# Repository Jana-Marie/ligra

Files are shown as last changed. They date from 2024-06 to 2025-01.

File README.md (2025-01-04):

# ligra

ligra is an open source image projector build from scratch and based off of flea market parts. ligra is not neccessarily a PCB-project nor a single thing, but rather an idea of how to design your own image-projection system. It is an introduction on how to create light-grafittis, how to share messages at large.

It's not strictly a Gobo, rather a way of building a system that may resemble one, but may also resemble a video projector or an abstract source of art. I have mostly used it with 2D printed stencils, usually used with so called "overhead projectors", one can of course also use metal-stencils, coloured effect-foils, 3D printed stencils and even LCDs, or really anything that may project an image. Get creative! 

<table>
  <tbody>
    <tr>
      <td>
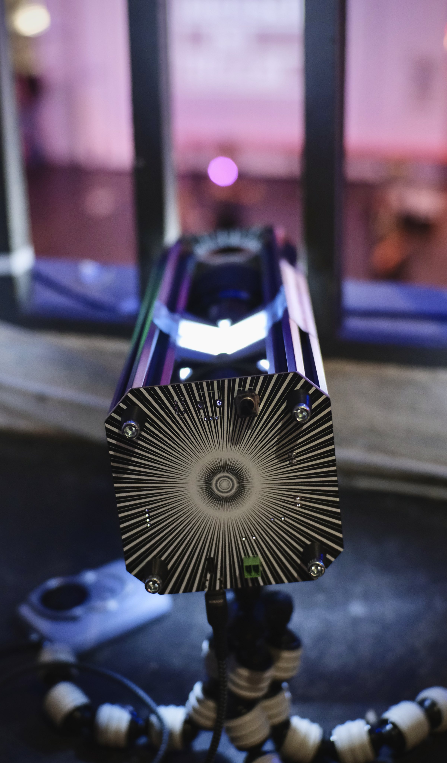
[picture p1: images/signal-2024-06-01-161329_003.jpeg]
        
      </td>
      <td>
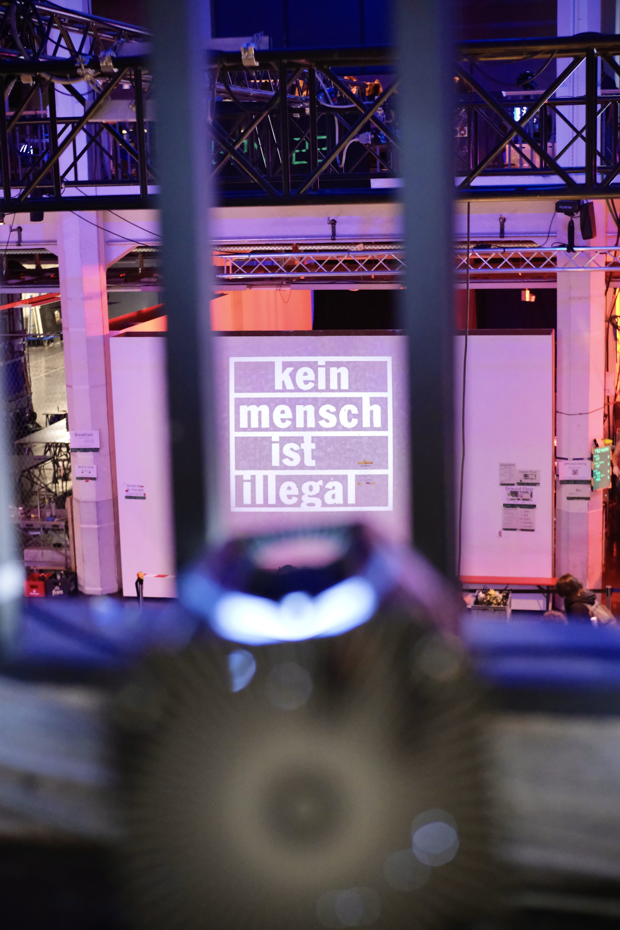
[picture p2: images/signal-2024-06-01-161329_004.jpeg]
        
      </td>
    </tr>
    <tr>
      <td colspan="2">
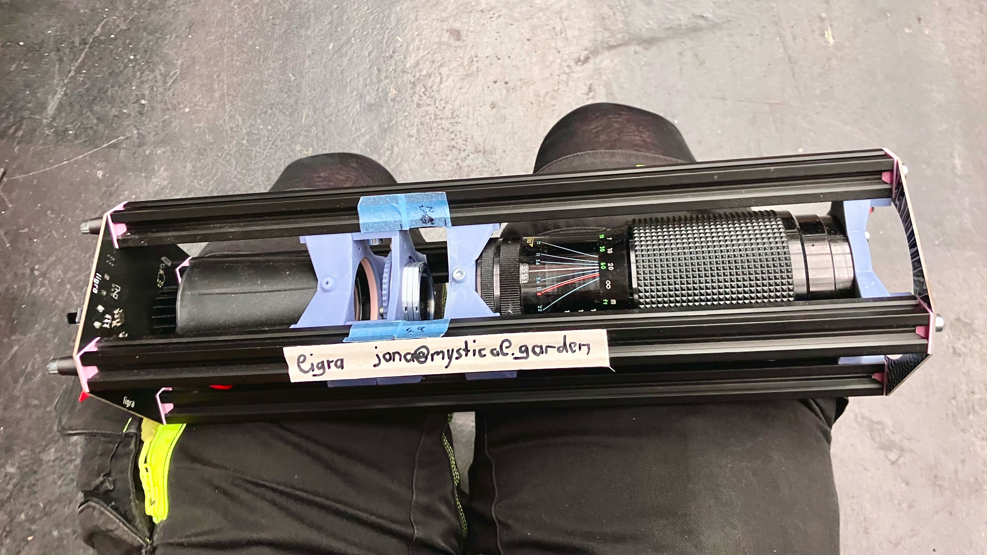
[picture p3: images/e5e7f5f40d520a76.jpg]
        
      </td>
    </tr>
  </tbody>
</table>

This repo is very WIP and shall be expanded soon :3

## Working principle

ligra essentially functions as a backwards camera, well, most projectors do. This becomes more visible when we talk about its inner workings, it's heart and most fixed element is the lens, a Canon FD lens in our case. But instead of using it to project and image **onto** a 35mm film slide, we will project light **through** a ruffly 35mm film slide-sized, image forming medium (i.e. a 2D printed stencil). This light will enter the lens from the back, projecting an image onto a scene with the properties of the lens (focal length, aperture and focus). Given the quality of even early lenses, we can expect some sharp and crisp projections. [WIP ...]

## [Instructions](https://github.com/Jana-Marie/ligra/blob/main/instructions.md)

(Want to build one? ^ click me)

<table>
  <tbody>
    <tr>
      <td>
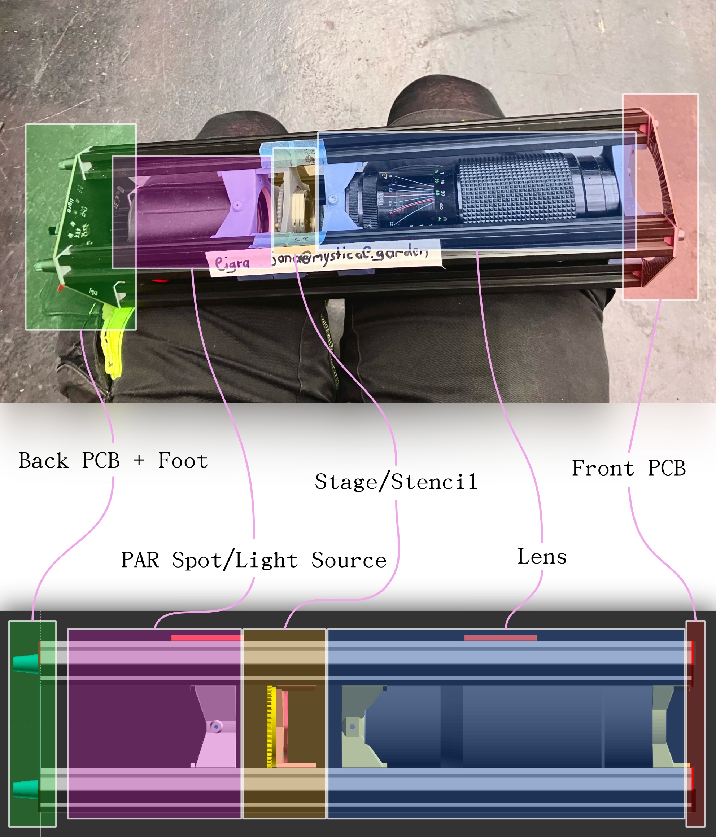
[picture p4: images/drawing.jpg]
        
      </td>
    </tr>
  </tbody>
</table>

## [Projection-Media](https://github.com/Jana-Marie/ligra/blob/main/projection-media.md)

(You have one and need stencils? ^ click me)

<table>
  <tbody>
    <tr>
      <td>
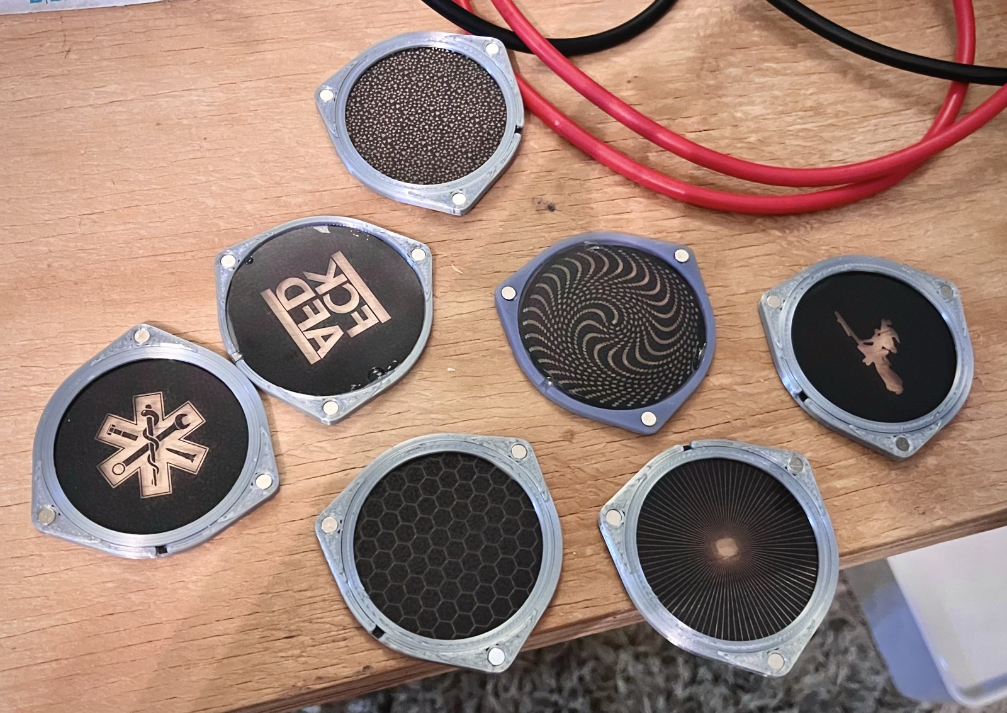
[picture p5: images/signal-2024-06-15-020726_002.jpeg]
        
      </td>
      <td>
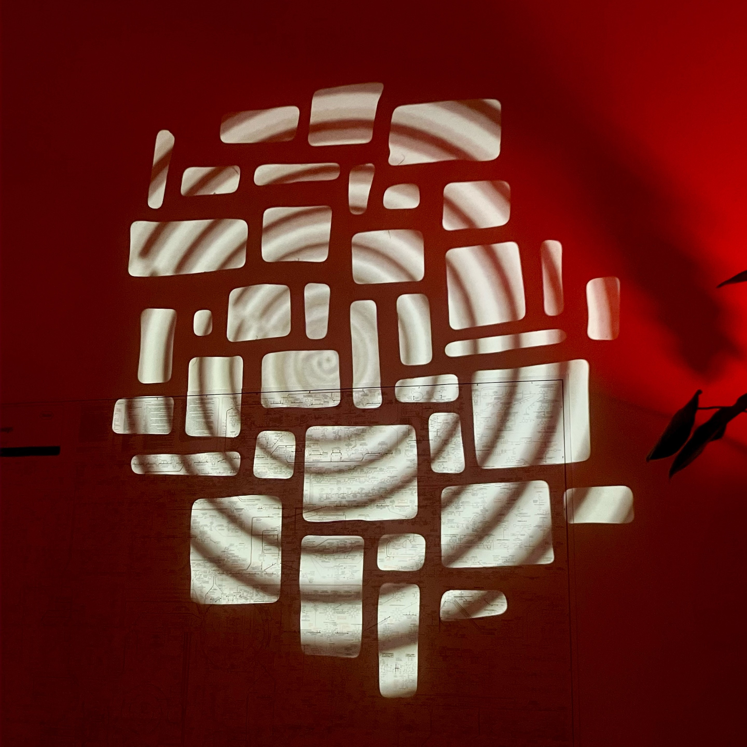
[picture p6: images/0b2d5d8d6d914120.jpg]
        
      </td>
      <td>
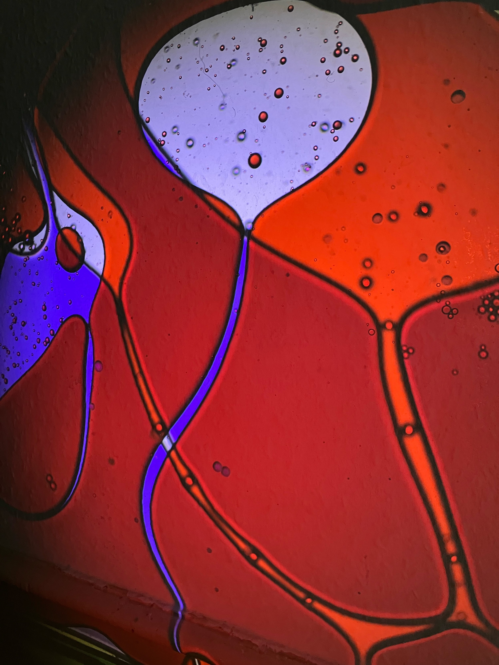
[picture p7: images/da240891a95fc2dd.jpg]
        
      </td>
    </tr>
  </tbody>
</table>

## [Staging-Stages](https://github.com/Jana-Marie/ligra/blob/main/staging-stages.md)

(You have one and want to work on a different stage, a different way of adding media for projection? ^ click me)

<table>
  <tbody>
    <tr>
      <td>
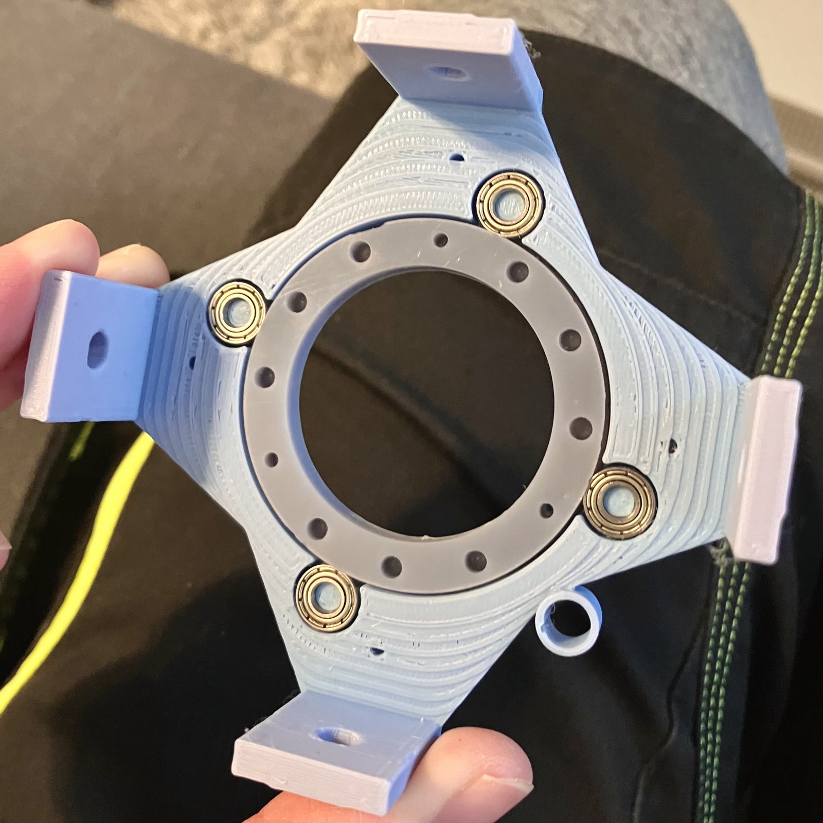
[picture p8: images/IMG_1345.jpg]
        
      </td>
      <td>
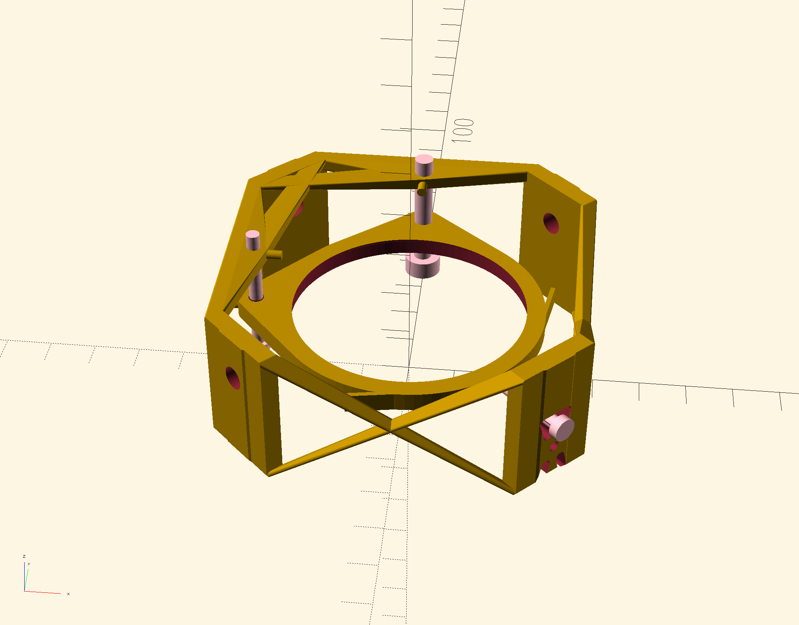
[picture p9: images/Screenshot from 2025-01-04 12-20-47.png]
        
      </td>
      <td>
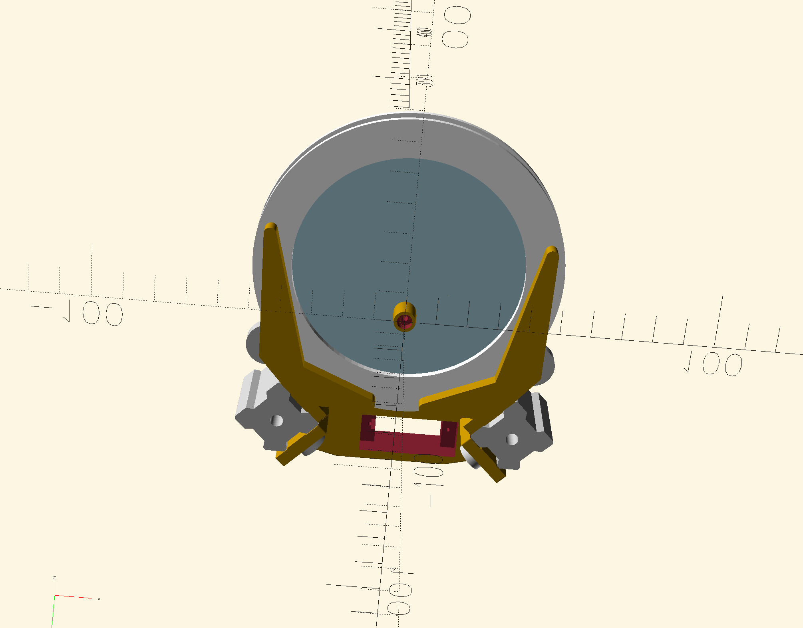
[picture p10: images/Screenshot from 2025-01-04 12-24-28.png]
        
      </td>
    </tr>
  </tbody>
</table>

## Todo

- [ ] Add assembly instructions (85% done)
  - [ ] Refine by adding real images (45% done)
- [ ] Add 3D print instructions (5% done)
- [ ] Add BOM (0% done)
- [ ] Add drawings (60% done)
- [x] Make projection-media page more expressive
- [x] Design more stages
- [x] Cleanup OpenSCAD file

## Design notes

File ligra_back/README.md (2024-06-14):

# Back-Board

This board serves as power-input and LED controller for a 0-3A 0-5V LED. It currently is v1.0.0 and has an additional DC-motor speed controller onboard, you can safely ignore it. I plan to build a different version for myself, that is a bit more advanced, feel free to then also use it. Generally this board is fully optional, but may prove to be very useful.

<table>
  <tbody>
    <tr>
      <td>
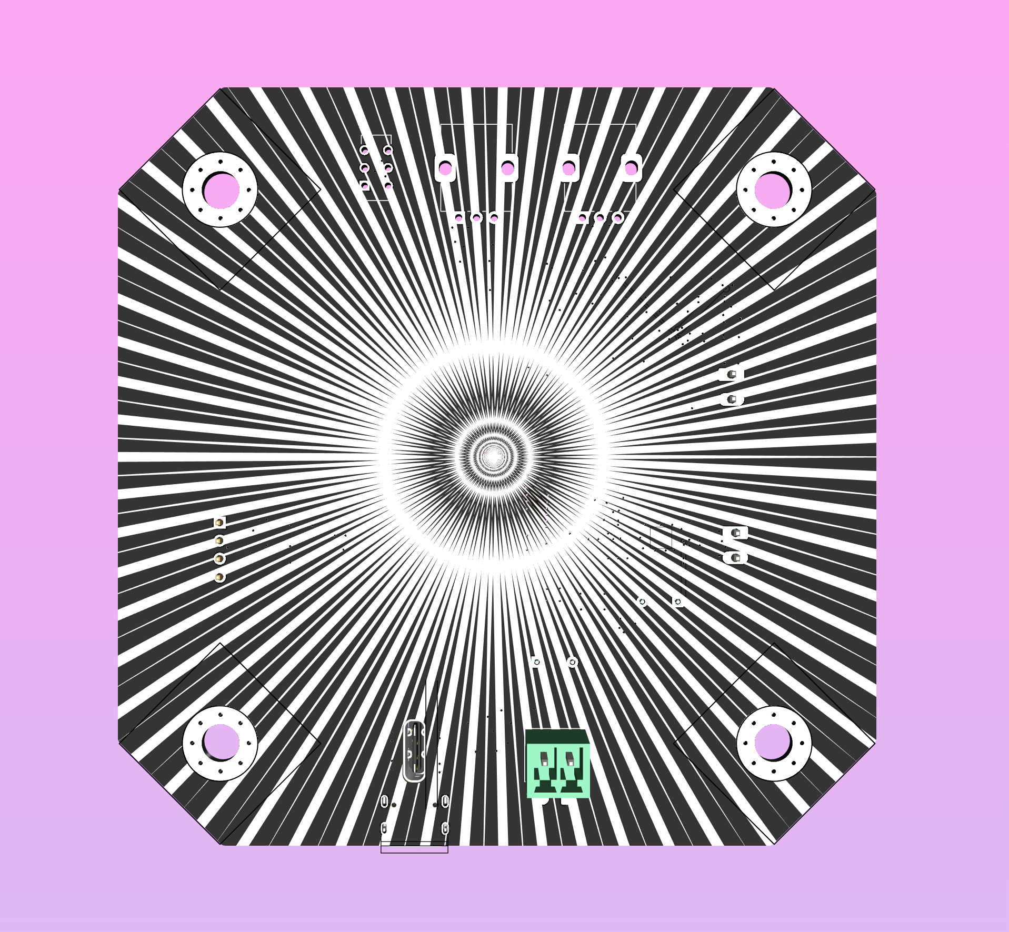
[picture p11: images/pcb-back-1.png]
        
      </td>
      <td>
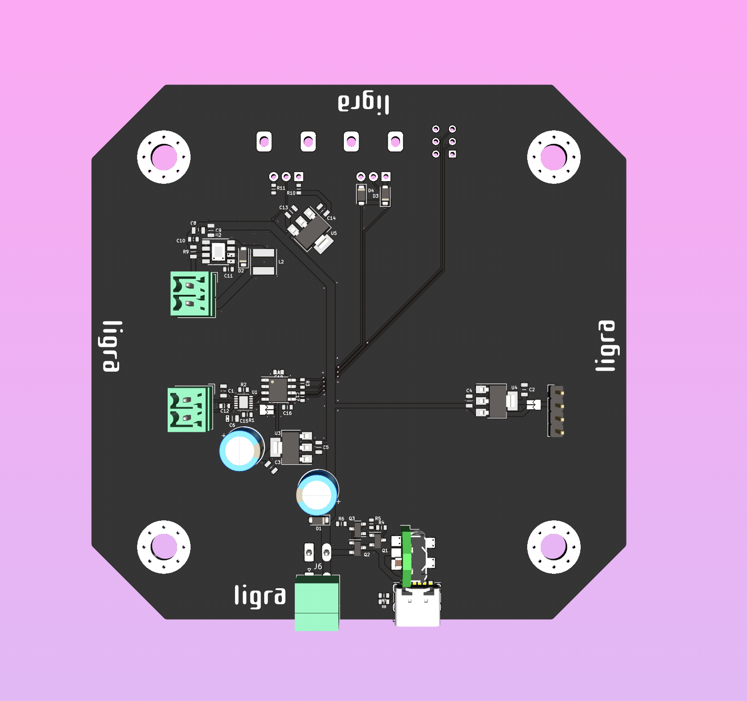
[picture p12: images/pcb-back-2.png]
        
      </td>
    </tr>
  </tbody>
</table>

[Todo, add BOM and assembly instructions here]

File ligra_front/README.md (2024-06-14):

# Front-Board

There is not a whole lot to say about this board, it serves no electrical function, merely an aesthetic one, as well as a protector against bumping into bare aluminium.

<table>
  <tbody>
    <tr>
      <td>
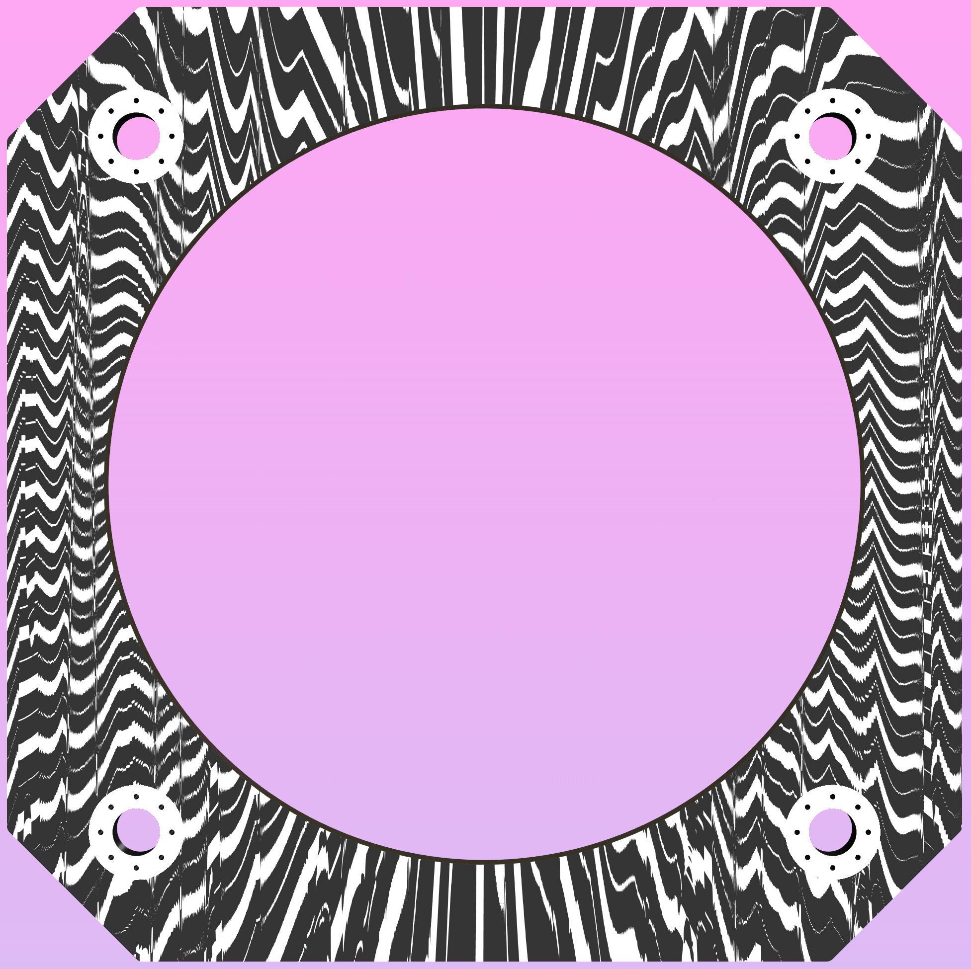
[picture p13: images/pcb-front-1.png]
        
      </td>
      <td>
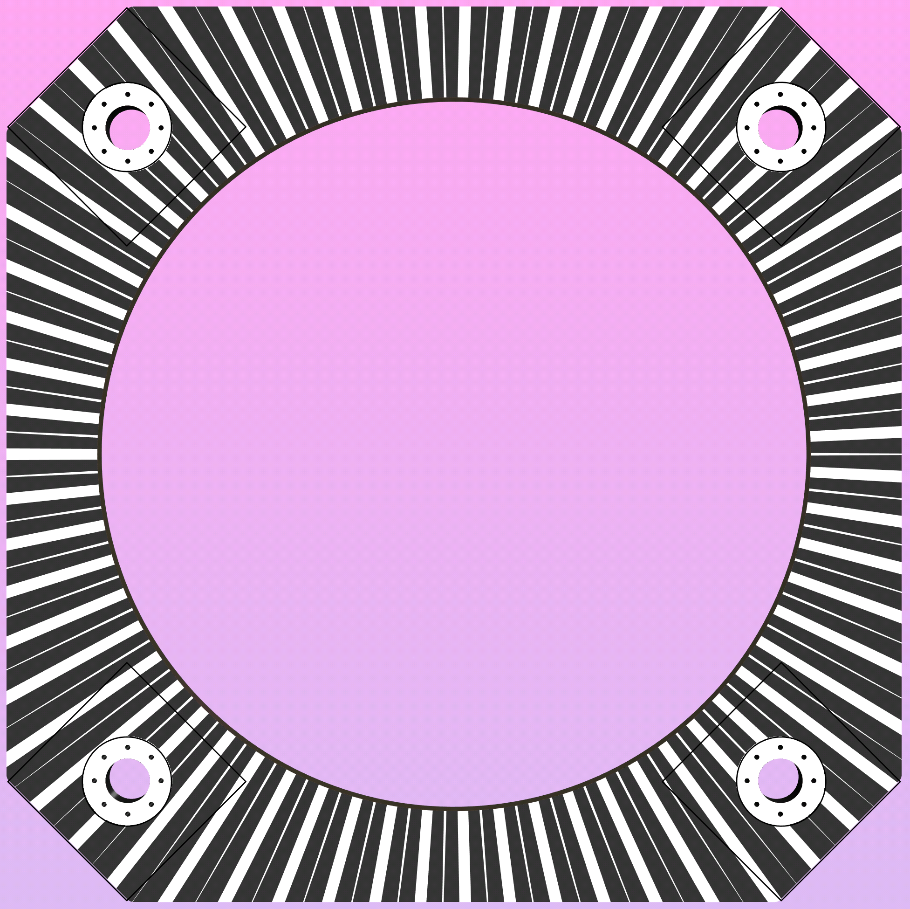
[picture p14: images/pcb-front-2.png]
        
      </td>
    </tr>
  </tbody>
</table>

Please order them with a thickness of 1.6mm.

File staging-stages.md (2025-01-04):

# Staging-Stages

There is of course more than one posssible stage, this page is here to collect ideas for different pages.

## Table of Contents

* [Open Ideas](#open-ideas)
* [Motor-Rotating Stage](#motor-rotating-stage)
* [3-Point Stage](#3-point-stage)
* [Oil Disc](#oil-disc)

## Open Ideas

 - [ ] 35mm Film Stage
 - [ ] Dia-Film Stage
 - [ ] Plexiglas-Block with Effect-Particles Inside
 - [ ] Effect-Foil 

## Motor-Rotating Stage

Please refer to [the instructions](https://github.com/Jana-Marie/ligra/blob/main/instructions.md#Stage) for this one, it is detailed there.

<table>
  <tbody>
    <tr>
      <td>
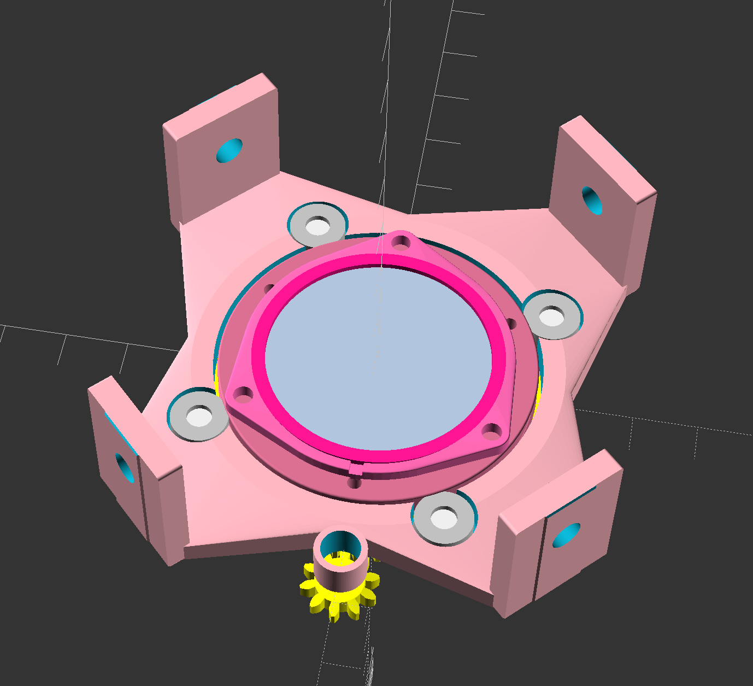
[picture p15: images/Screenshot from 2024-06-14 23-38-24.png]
        
      </td>
      <td>
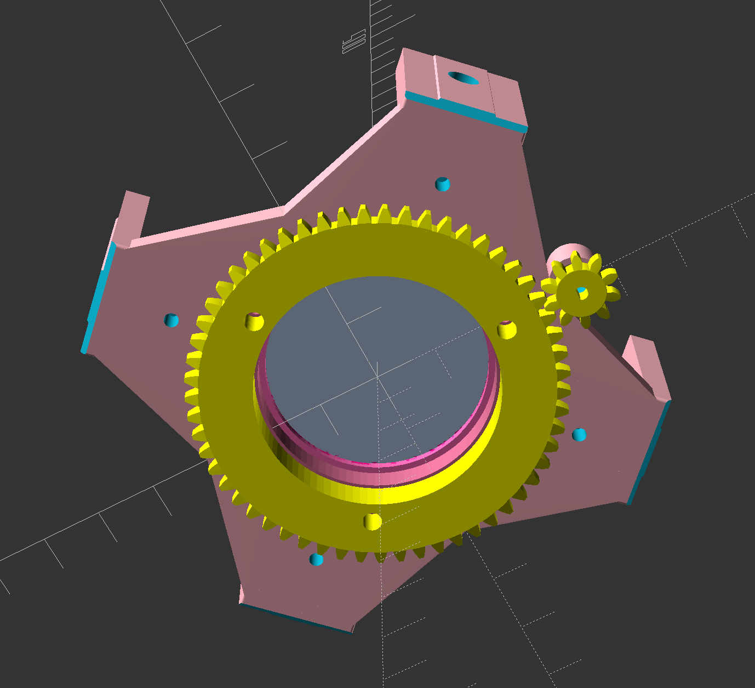
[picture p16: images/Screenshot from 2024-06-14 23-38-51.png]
        
      </td>
    </tr>
  </tbody>
</table>

## 3-Point Stage

My earliest attempt, make a 3-point connected stage for trapez-correction. I designed and built one, it worked, but was so flimsy. Didn't keep on improving it, but eventually an overhaul is due.

<table>
  <tbody>
    <tr>
      <td>
        
      </td>
      <td>
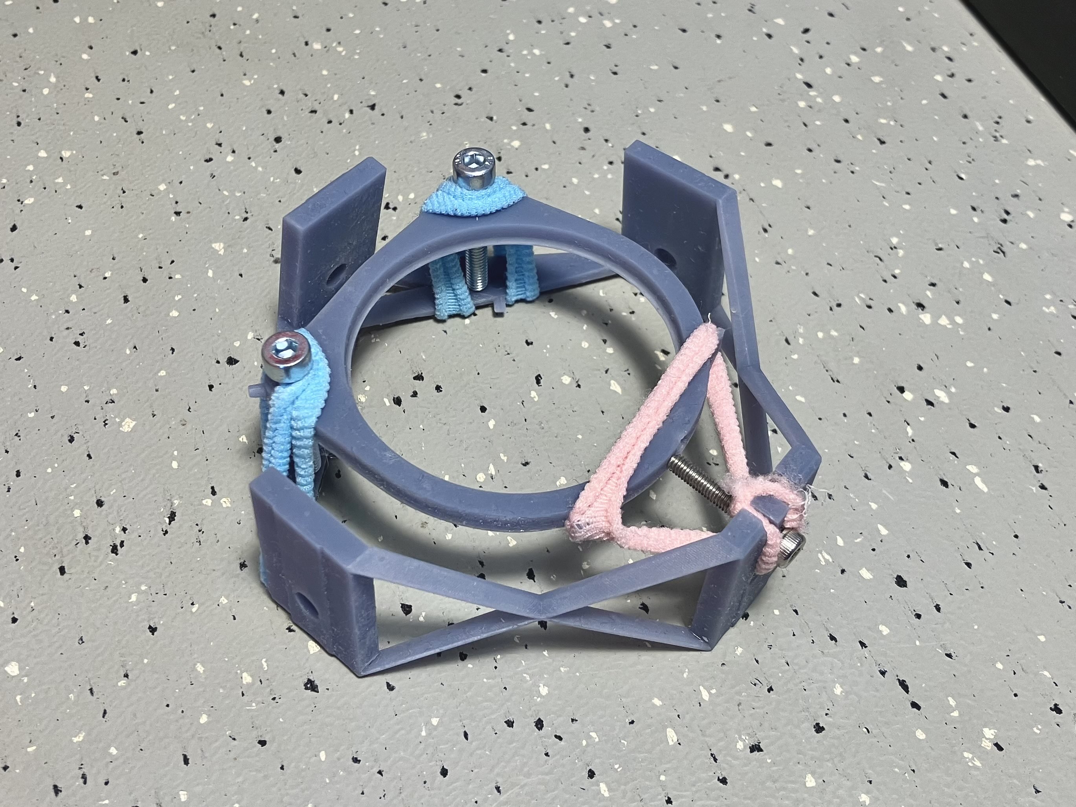
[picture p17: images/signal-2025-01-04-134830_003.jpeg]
        
      </td>
    </tr>
  </tbody>
</table>

## Oil Disc

Another fun stage is to use a 70s style oil disc. They are available from Mathmos or used on ebay, but require some modification to the whole frame.

<table>
  <tbody>
    <tr>
      <td>
        
      </td>
      <td>
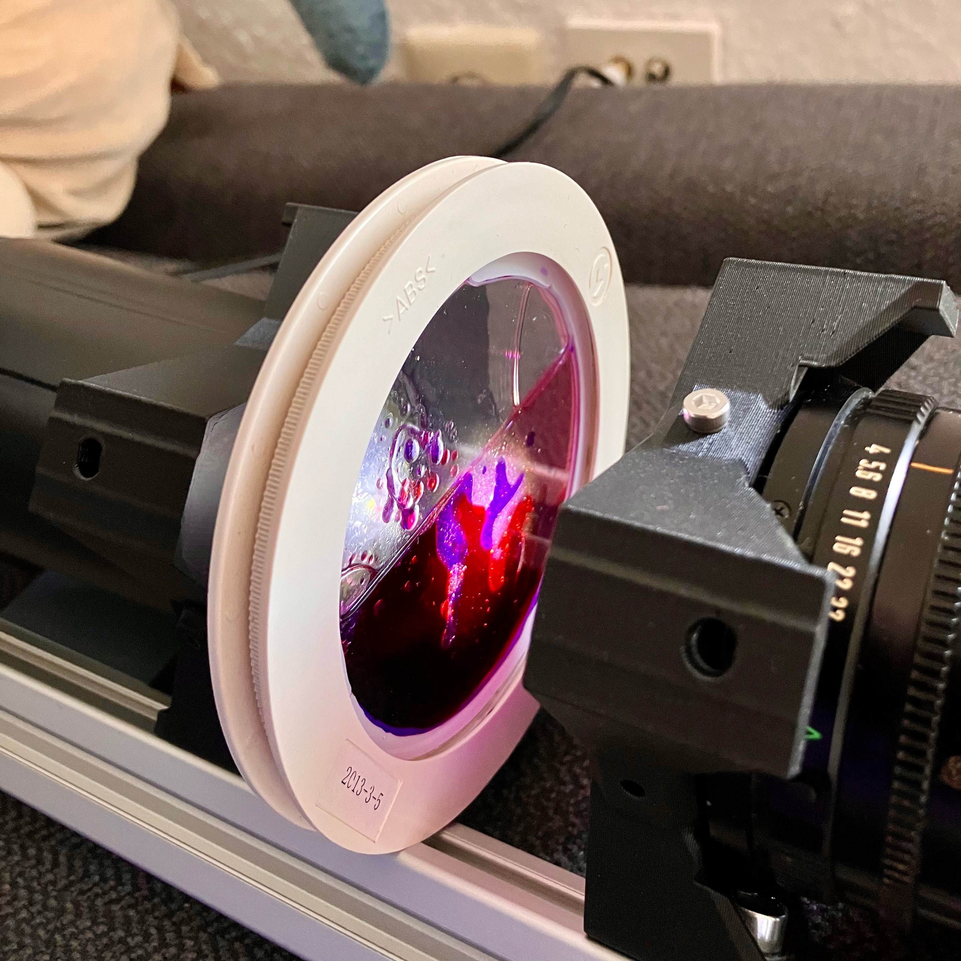
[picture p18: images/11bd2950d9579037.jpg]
        
      </td>
    </tr>
    <tr>
      <td>
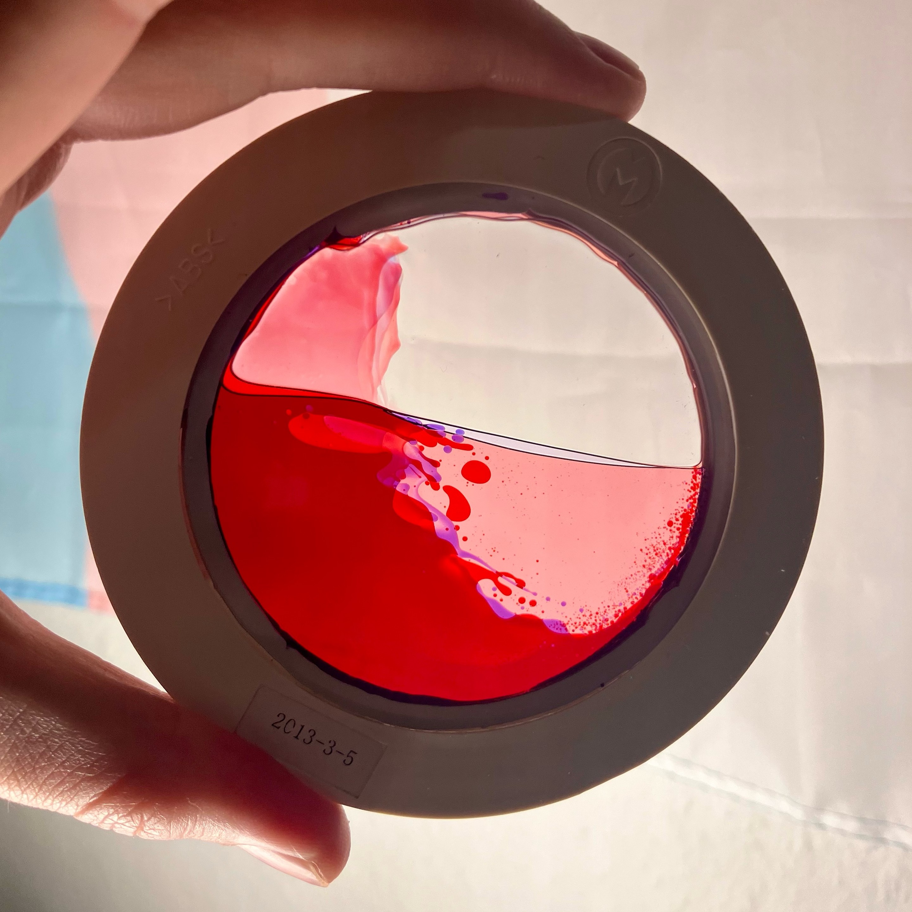
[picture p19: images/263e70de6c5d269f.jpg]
        
      </td>
      <td>
        
      </td>
    </tr>
  </tbody>
</table>

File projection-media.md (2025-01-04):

# Projection-Media

A collection of different projection-media ideas.

Similar to a camera, where only a part of the imaged are is in focus on the sensor, only a narrow band of projection media becomes sharp on your projection site. This is both a disatvantage as we have to move our focus to get our subject to appear sharp, as well as an advantage. Our subject becomes really sharp, sharper than many projectors can do and we can play with focus.

## Table of Contents

* [2D Print](#2d-print)
  * [Step prints](#step-prints)
* [Metal-Stencil](#metal-stencil)
* [2.5D Print](#2.5d-print)
* [Oil Disc](#Oil-Disc)
* [LCD](#lcd)

## 2D Print

Arguably the most easy and fast way is to 2D print a stencil on laser or inkjet printer. To do so, you will need to buy some printable foil, take note that it must be compatible with the printing technology (i.e. laser/toner, inkjet, riso??, ...) available to you. Sometimes such foil is called "overhead-projector media". You can find a template in [`/stencils/`](/stencils/2D_stencil_print.svg), called `2D_stencil_print.svg`. It is compatible with the [stage mentioned in the instructions](https://github.com/Jana-Marie/ligra/blob/main/instructions.md#Stage).

You will find 24 black circles in the document, place your design within the green border that is visible on these black dots. Note that there will be considerable vignetting towards their edges, center your designs well and keep some distance. I've left four designs as an example. Everything white will become visible/illuminated, everything black will be blocked out and everything inbetween will be visible as inbetween. Get creative! Oh and one last thing, turn off the visibility of the "Visible Media" layer before printing to dinA4, it is meant as a guide and is not to be printed.

<table>
  <tbody>
    <tr>
      <td>
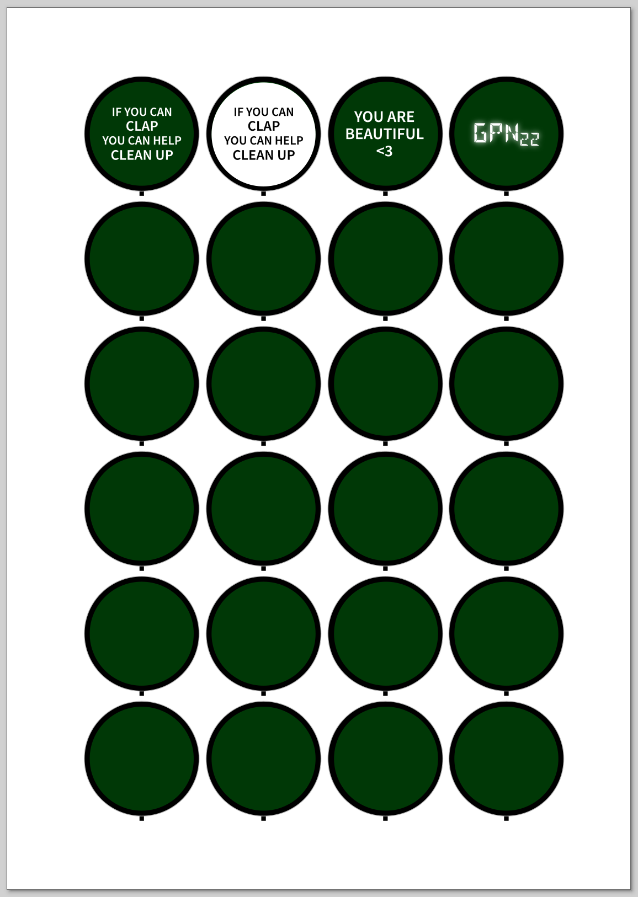
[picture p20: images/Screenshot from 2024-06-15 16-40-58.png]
        
      </td>
      <td>
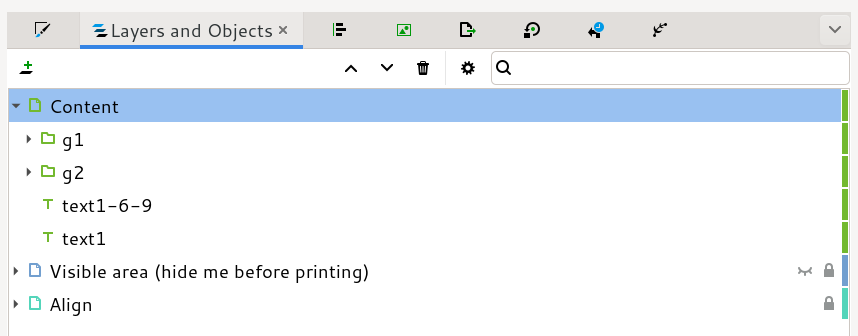
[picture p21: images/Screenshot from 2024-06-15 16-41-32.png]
        
      </td>
      <td>
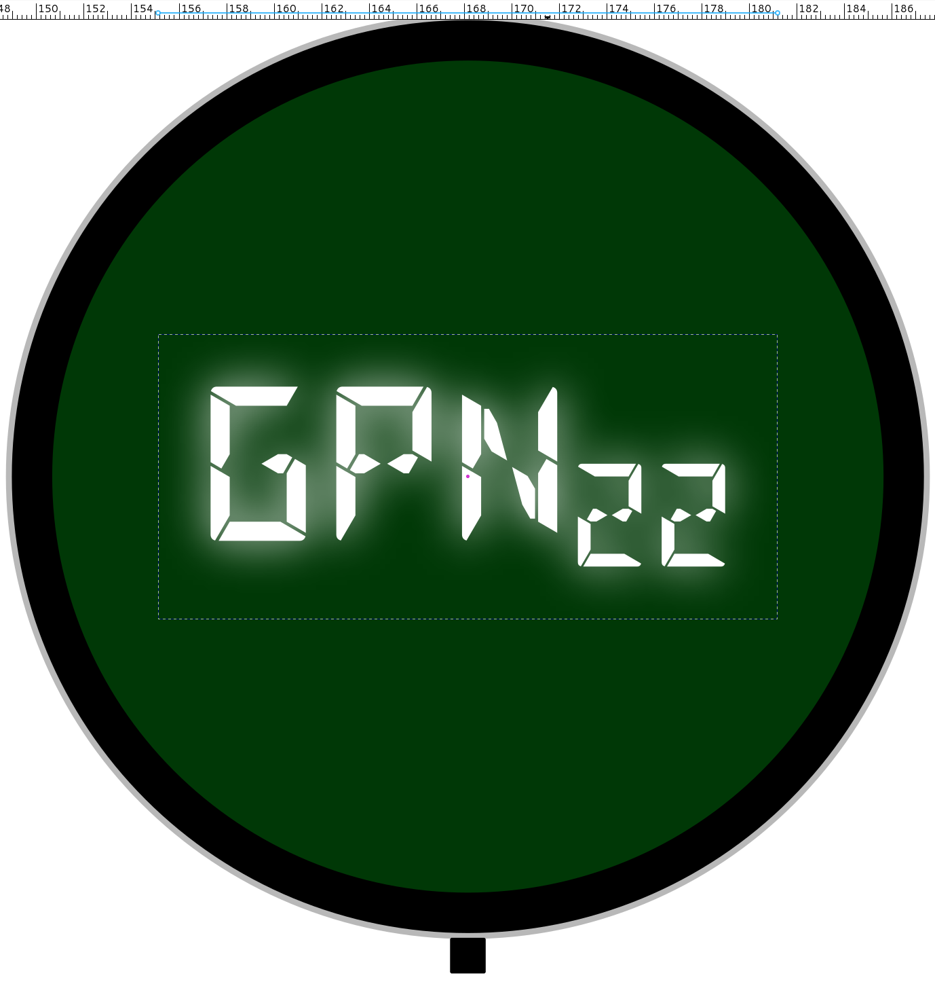
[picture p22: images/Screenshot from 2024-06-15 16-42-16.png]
        
      </td>
    </tr>
  </tbody>
</table>

### Step prints

You can also stack multiple stencils, moving them in the focal plane of the projector. With this you can create blurry backgrounds or sceneries, while maintaining sharper subjects.

<table>
  <tbody>
    <tr>
      <td>
        
      </td>
    </tr>
  </tbody>
</table>

## Metal stencil

Instead of a 2D printed stencil, you can of course also design and buy a metal stencil from a PCB/Stencil vendor like JLCpcb, PCBway, AllPCB, OSHStencils and others.

Furthermore, you can head over to AliExpress and other vendors to buy pre-made Gobo-Projector stencils, [like these.](https://www.aliexpress.com/item/1005004907991627.html). A diameter between 37.5mm to 25mm should work, ~36mm is an ideal size. Please adapt the [stencil cage](https://github.com/Jana-Marie/ligra/blob/main/instructions.md#Stage) mentioned in the stage section accordingly.

<table>
  <tbody>
    <tr>
      <td>
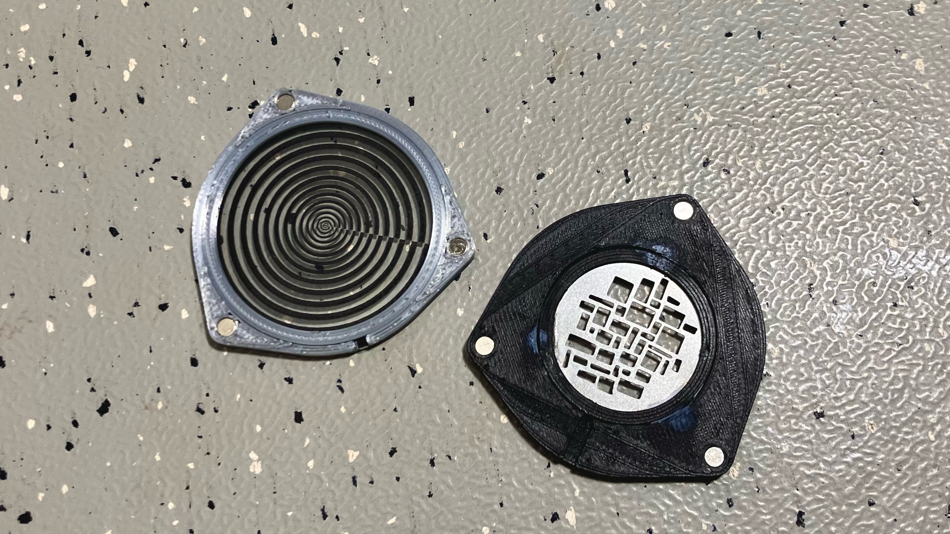
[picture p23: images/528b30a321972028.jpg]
        
      </td>
    </tr>
  </tbody>
</table>

## 2.5D Print

If you have a 3D printer, which you likely do if you are replicating this, you can of course directly print a stencil on the printer itself, with the filament you are using to print the stencil cage. Never tried this though..

## LCD

Lastly, this is on my todo list, you can of course replace the whole static stencil with an LCD screen (or any other light disrupting display technology). Would love to know how this looks like.

## Oil Disc

Another fun projection media are oil disks, from e.g. Mathmos. They require some modification to the frame as they are usually too big to fit and need to rotated constantly.

<table>
  <tbody>
    <tr>
      <td>
        
      </td>
      <td>
        
      </td>
      <td>
        
      </td>
    </tr>
  </tbody>
</table>

## Other ideas?

Any other ideas? Pleeeease send them to me, would love to test them.

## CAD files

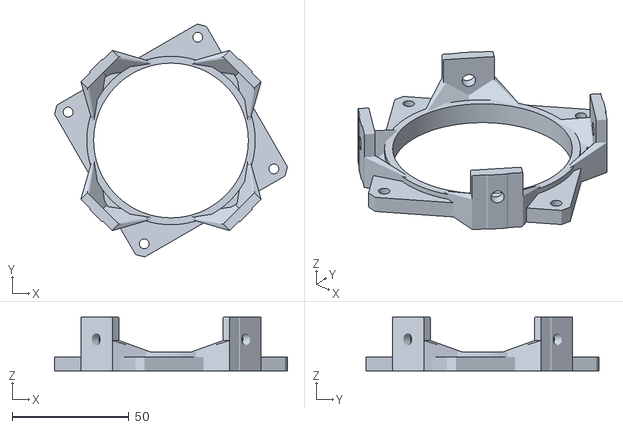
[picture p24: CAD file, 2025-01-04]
CAD/stls/ligra_projectorlens.stl
99.6 x 99.6 x 23.0

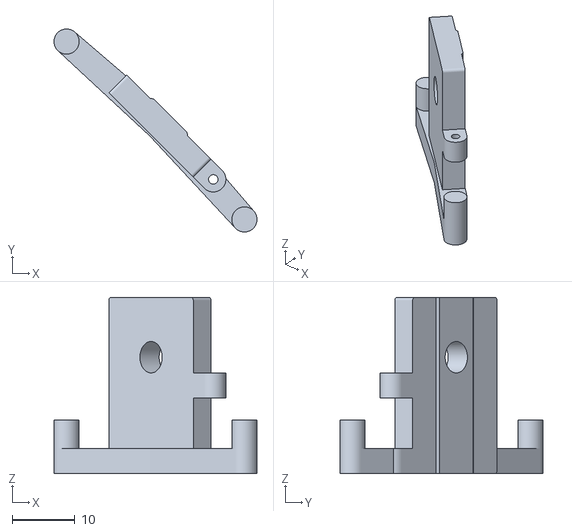
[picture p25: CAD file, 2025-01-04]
CAD/stls/ligra_lava_disk_bracket.stl
32.3 x 32.3 x 28.0

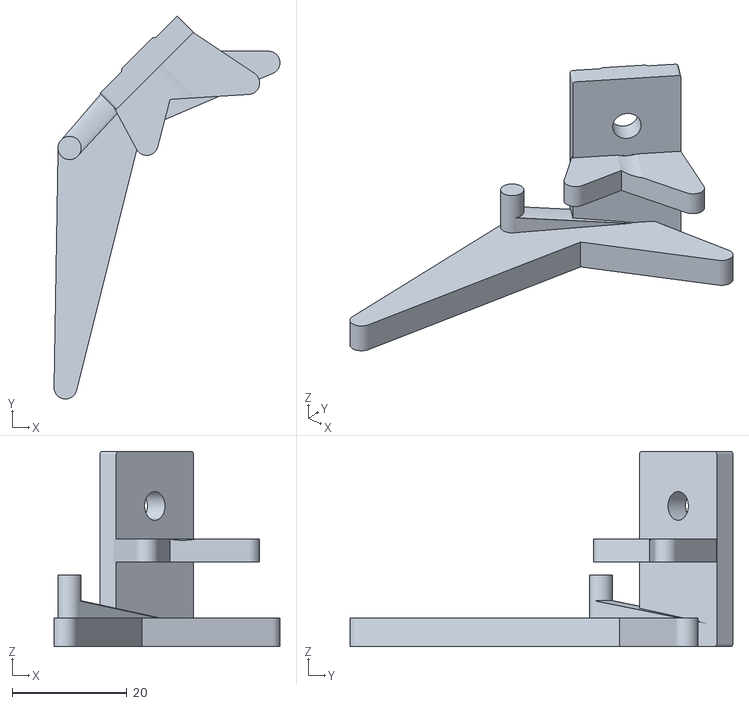
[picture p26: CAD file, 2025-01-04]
CAD/stls/ligra_lava_disk_arm_r.stl
39.4 x 66.7 x 34.0

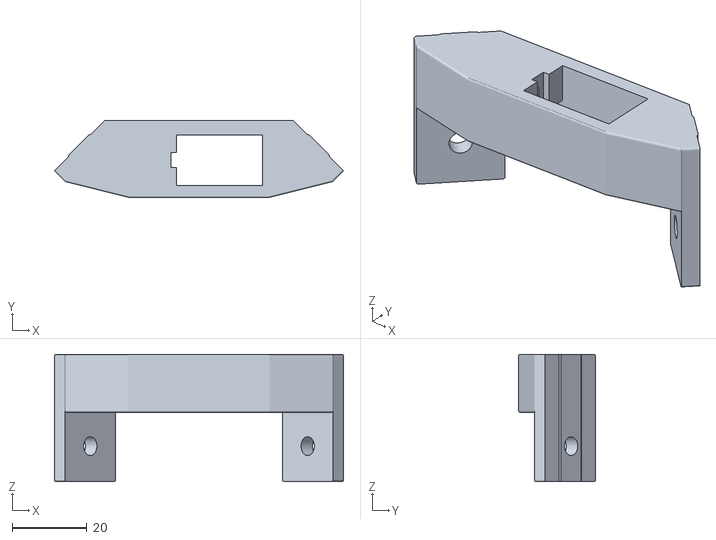
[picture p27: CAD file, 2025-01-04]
CAD/stls/ligra_lava_disk_motor_mount.stl
77.1 x 20.5 x 34.0

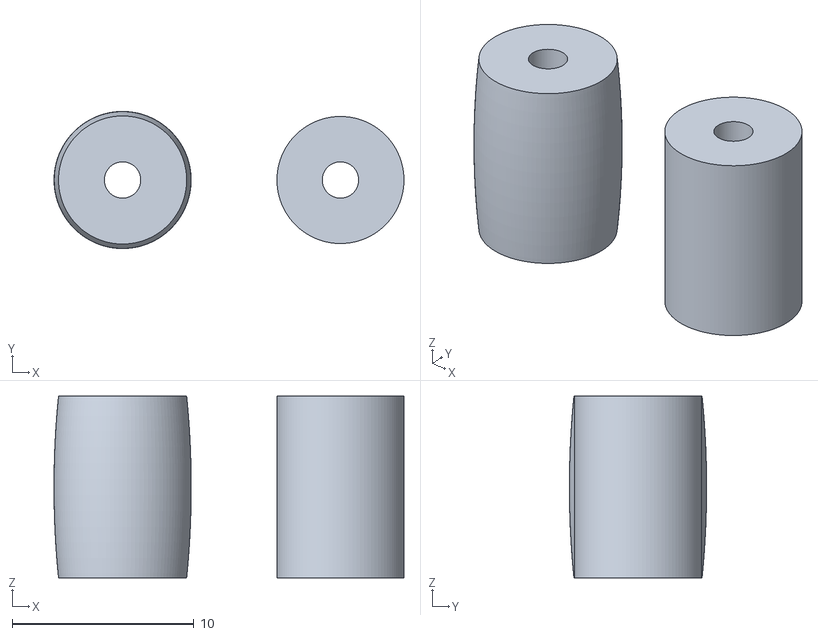
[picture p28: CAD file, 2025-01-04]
CAD/stls/ligra_lava_disk_servo_shaft.stl
19.3 x 7.56 x 10.0

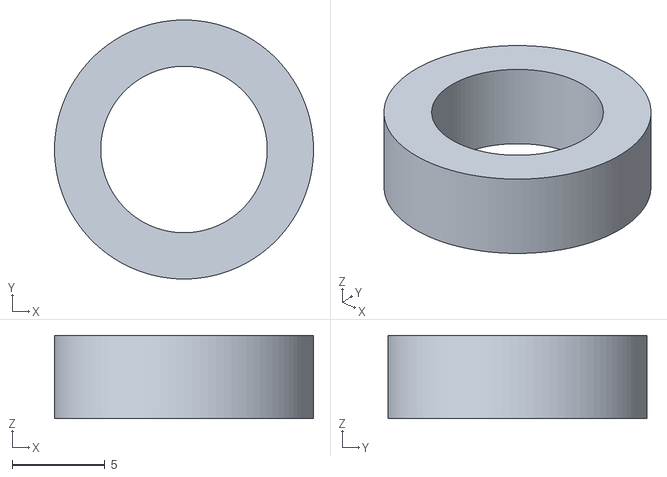
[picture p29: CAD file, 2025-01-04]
CAD/stls/ligra_lava_disk_rolls.stl
14.0 x 14.0 x 4.50

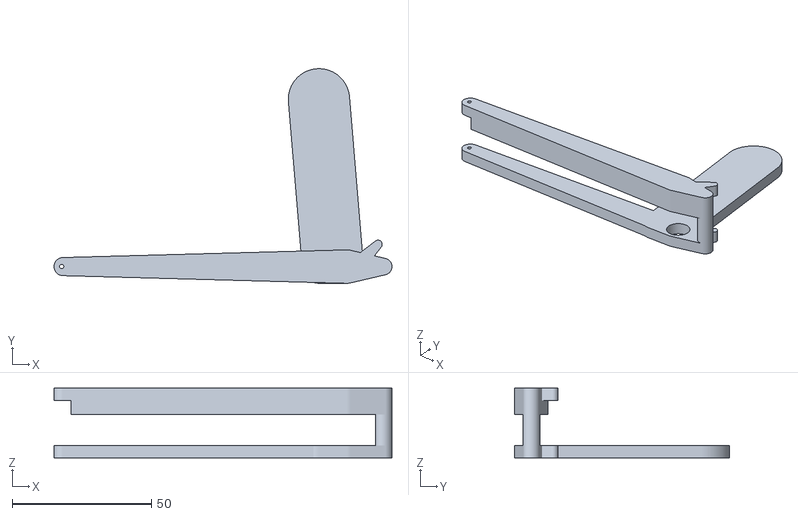
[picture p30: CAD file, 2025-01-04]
CAD/stls/ligra_lava_disk_arm.stl
121.2 x 77.0 x 25.0

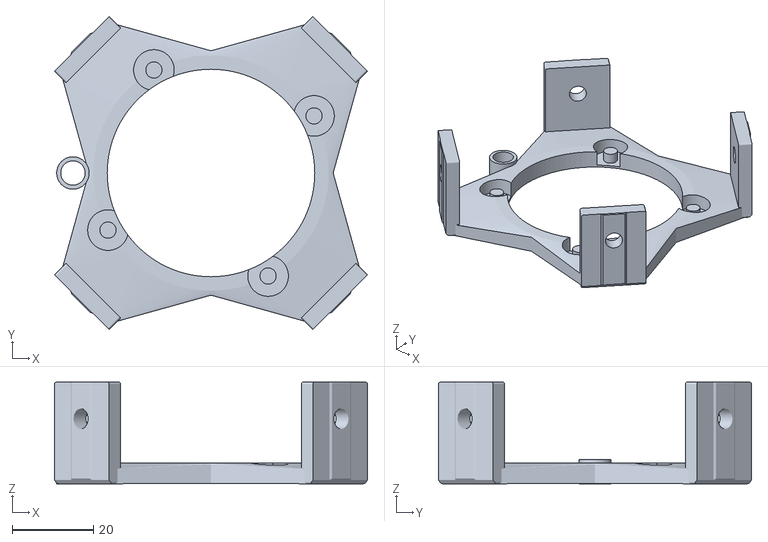
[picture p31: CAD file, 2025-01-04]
CAD/stls/ligra_stage_stage_motor_rot_base.stl
77.1 x 77.1 x 25.0

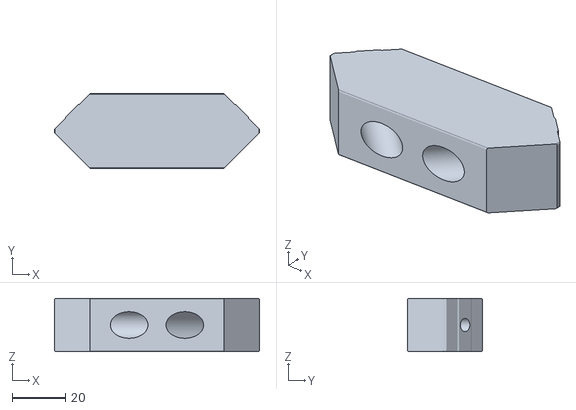
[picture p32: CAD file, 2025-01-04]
CAD/stls/ligra_interlock.stl
77.1 x 28.1 x 20.0

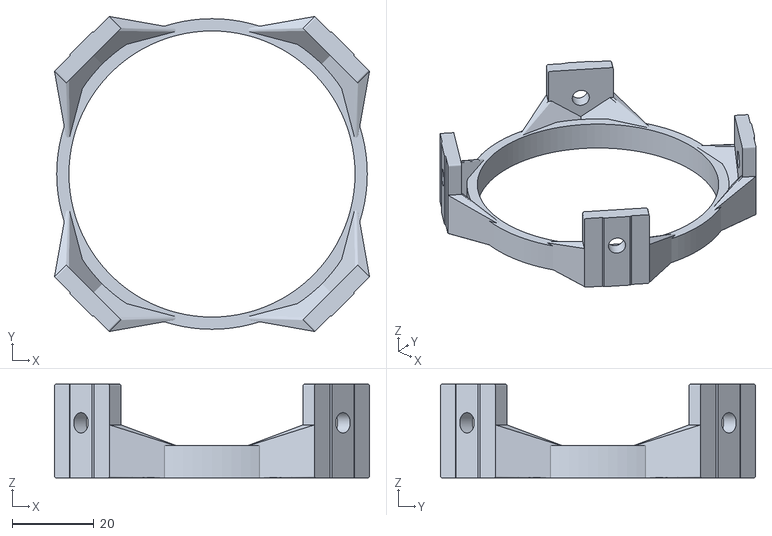
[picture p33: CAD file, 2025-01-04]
CAD/stls/ligra_lens_frontcap_38-95.stl
77.1 x 77.1 x 23.0

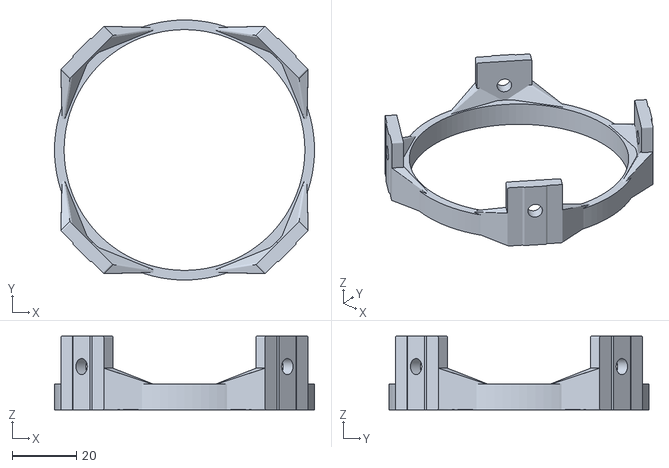
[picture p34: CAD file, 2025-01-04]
CAD/stls/ligra_lens_frontcap_35-105.stl
81.0 x 81.0 x 23.0

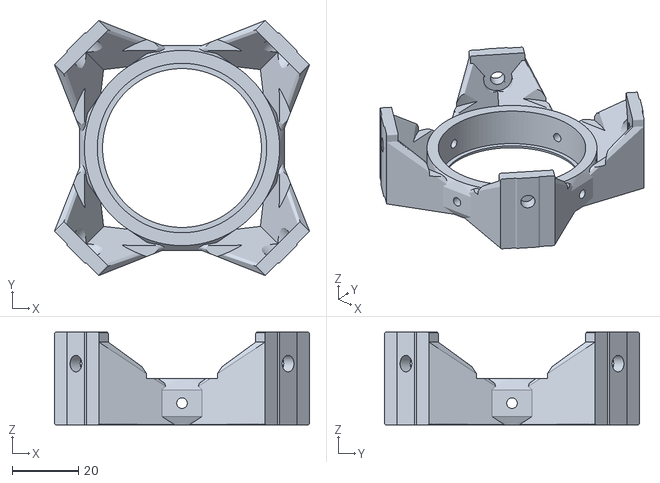
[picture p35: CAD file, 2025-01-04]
CAD/stls/ligra_lens_lenscagefd.stl
77.1 x 77.1 x 28.0

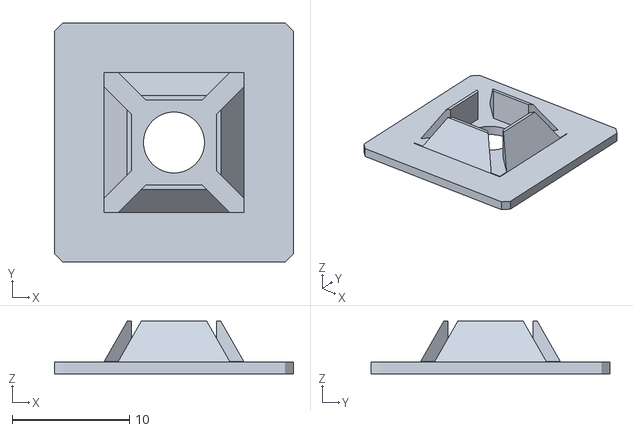
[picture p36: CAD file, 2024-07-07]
CAD/stls/ligra_misc_cap.stl
20.4 x 20.4 x 4.50

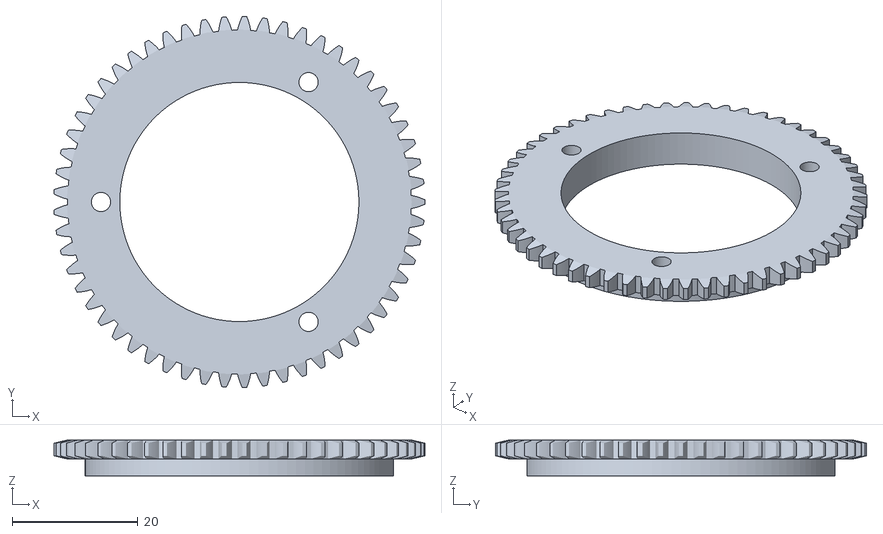
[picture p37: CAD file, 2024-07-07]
CAD/stls/ligra_stage_stage_motor_rot_gear_l.stl
59.0 x 59.0 x 5.70

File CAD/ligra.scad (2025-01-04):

use <ligra_flashlight.scad>
use <ligra_par_spot.scad>
use <ligra_tripod.scad>
use <ligra_lens.scad>
use <ligra_stage.scad>
use <ligra_lava_disk.scad>
use <ligra_frame.scad>
use <ligra_misc.scad>

// nya! Welcome to the 3D planning & design file of ligra
// use this file to plan your porjector, see the two pre-planned-
// projectors (28_80_300 & 70_210_400) below. Use all the files in this
// directory to design and adapt custom parts. You can work on the parts
// in their respective files and just use them here afterwards.
// That should keep everything easy to understand and fast to work on.
// Please plan your files (F5) in the $preview clause and add them to the
// 'else' clause for rendering (F6).
// Enjoy~
// 
// - Jana

if($preview){
    // Canon FD 28-80mm base projector, PAR Spot, rot-stencil stage, 300mm frame
    translate([-70,0,60])rotate([80,0,0])translate([0,0,-150])projector_28_80_300();
    
    // Canon FD 70-210mm base projector, PAR Spot, rot-stencil stage, 400mm frame
    translate([ 70,0,60])rotate([80,0,0])translate([0,0,-150])projector_70_210_400();
} else{
}

// Canon FD 28-80mm base projector, PAR Spot, rot-stencil stage, 300mm frame
module projector_28_80_300(){
    $fn=60;
    offx=170;
    
    // frame
    color("silver")frame(300,45);
    
    // lens
    color("Khaki")translate([0,0,offx])lenscage_fd(45);
    color("Khaki")translate([0,0,offx+98+6])frontcage_fd_28_80(45);
    
    translate([0,0,offx+1])lenscap_fd();
    translate([0,0,offx+1+13.6])lens_fd_28_80();
    
    // tripod mount
    color("Tomato")translate([0,0,160])tripod_plate(45);

    // stencil stage
    translate([0,0,offx-40])stage_motor_rot_assembly(45);
    
    // PAR Spot
    translate([0,0,120])rotate([180,0,0])par_spot_cage(45);
    
    // PCB
    color("DarkslateGray")translate([0,0,302.6])rotate([180,0,0])front_pcb();
    color("DarkslateGray")translate([0,0,-1])rotate([180,0,0])back_pcb();
    
    
    for(i=[-1:2:1],j=[-1:2:1]){
        // foot
        color("DarkTurquoise")translate([i*38.6,j*38.6,-1.6])rotate([180,0,0])foot();
        // cap
        color("Red")translate([i*38.6,j*38.6,-2])rotate([0,0,45])cap();
        color("Red")translate([i*38.6,j*38.6,302])rotate([180,0,45])cap();
    }
    
    // Obsolete, flashlight light source
    *translate([0,0,20])flashlight();
    *color("Olive")translate([0,0,166])flashlight_cage(45);
    *color("Olive")translate([0,0,100])flashlight_counter();
}

// Canon FD 70-210mm base projector, PAR Spot, rot-stencil stage, 400mm frame
module projector_70_210_400(){
    $fn=60;
    offx=185;
    // frame
    color("silver")frame(400,45);
    
    // lens
    color("Khaki")translate([0,0,offx])lenscage_fd(45);
    color("Khaki")translate([0,0,offx+185+6])frontcage_fd_70_210(45);

    translate([0,0,offx+1])lenscap_fd();
    translate([0,0,offx+1+13.6])lens_fd_70_210();
    
    // tripod mount
    color("Tomato")translate([0,0,260])tripod_plate(45);
    color("Tomato")translate([0,0,80])tripod_plate(45);
    
    // stencil stage
    translate([0,0,offx-40])stage_motor_rot_assembly();
    
    // PAR Spot
    translate([0,0,120])rotate([180,0,0])par_spot_cage(45);
    
    // PCB
    color("DarkslateGray")translate([0,0,402.6])rotate([180,0,0])front_pcb();
    color("DarkslateGray")translate([0,0,0])rotate([180,0,0])back_pcb();
    
    for(i=[-1:2:1],j=[-1:2:1]){
        // foot
        color("DarkTurquoise")translate([i*38.6,j*38.6,-1.6])rotate([180,0,0])foot();
        // cap
        color("Red")translate([i*38.6,j*38.6,-2])rotate([0,0,45])cap();
        color("Red")translate([i*38.6,j*38.6,402])rotate([180,0,45])cap();
    }
    
    // Obsolete, flashlight light source
    *translate([0,0,20])flashlight();
    *color("Olive")translate([0,0,166])flashlight_cage(45);
    *color("Olive")translate([0,0,100])flashlight_counter();
}

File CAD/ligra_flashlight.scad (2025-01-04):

$fn=100;

// flashlight file
//
// my first light source, a good one even, a simple flashlight

if($preview){
    translate([0,0,-146])flashlight();
    color("DeepPink")translate([0,0,0])flashlight_cage(45);
    color("HotPink")translate([0,0,-52])flashlight_counter();
} else {
    flashlight_cage(45);
    *flashlight_counter();
}

module flashlight(){
    difference(){
        union(){
            color("SlateGray")translate([0,0,5])cylinder(d=29.6,h=160-5);
            color("SlateGray")translate([0,0,160-39])cylinder(d=38,h=39);
            color("SlateGray")translate([0,0,160-39-17])cylinder(d2=38,d1=30,h=17);
            color("SlateGray")translate([0,0,160-39-17])cylinder(d2=38,d1=30,h=17);
            color("SlateGray")translate([0,0,5])resize(newsize=[29.6,29.6,10]) sphere(r=10);
        }union(){
            translate([0,0,160-9])cylinder(d=36,h=10);
        }
    }
    color("AliceBlue")translate([0,0,160-5])resize(newsize=[36,36,8]) sphere(r=10);
}

module flashlight_cage(spacing=45){
    // corner
    ch = 28;
    wt = 4;
    difference(){
        union(){
            for(i = [0:90:270]){
                // corner
                rotate([0,0,45+i])translate([spacing-wt/2-1/2,0,ch/2])
                minkowski(){
                    cube([wt-1,19-1,ch-1],center=true);
                    rotate([0,90,0])cylinder(d=1,h=1);
                }
                hull(){
                    rotate([0,0,45+i])translate([spacing-wt/2,0,ch/2])cube([wt,8.5,ch],center=true);
                    rotate([0,0,45+i])translate([spacing-wt/2+0.33/2,0,ch/2])cube([wt+0.33,7.5,ch],center=true);
                }
                
                // middle sec
                cylinder(d=38.1+8,h=18);
                // connectors
                for(j = [-1:2:1]){
                    hull(){
                        rotate([0,90,45+i])translate([-0.5,19/2-0.5,spacing-wt])cylinder(d=1,h=wt);
                        rotate([0,90,45+i])translate([-0.5,-19/2+0.5,spacing-wt])cylinder(d=1,h=wt);
                        rotate([0,0,45+i])translate([spacing-wt/2,(-19/2+0.5)*j,0.5+24])cube([wt,1,1],center=true);
                        rotate([0,0,45+i-45*j])translate([(38.1+3)/2,0,0])cylinder(d=2,h=17);
                    }
                }
            }
            
            
        }union(){
            // corner
            for(i = [0:90:270]){
                rotate([0,90,45+i])translate([-ch+9.5,0,spacing-wt-1])cylinder(d=5,h=wt+2);
                rotate([0,90,45+i])translate([-ch+9.5,0,spacing-wt-wt-0.01])cylinder(d=10,h=wt);
                
                rotate([0,0,45+i])translate([0,30,20])cube([30,2,4],center=true);
            }
            // middle sec
            translate([0,0,-1])cylinder(d=38.1,h=17);
            translate([0,0,14])cylinder(d=36,h=5);
        }
    }
}

module flashlight_counter(){
    difference(){
        union(){
            cylinder(d=36,h=10);
            for(i = [0:90:270]){
                hull(){
                    rotate([0,0,45+i-10])translate([33/2,0,8])cylinder(d=3,h=2);
                    rotate([0,0,45+i+10])translate([33/2,0,8])cylinder(d=3,h=2);
                    rotate([0,0,45+i])translate([45/2,0,1])cylinder(d=2,h=2);
                }
            }
        }union(){
            translate([0,0,-0.5])cylinder(d=30,h=20);
        }
    }
}

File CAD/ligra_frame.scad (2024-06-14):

$fn=100;

// frame & extrusion file
//
// the extrusions and frame are generated in here

frame(100);

// Base frame
module frame(l=10,spacing=45){
    b = spacing/sin(45);
    echo("a = ", spacing);
    echo("b = ", b);
    echo("h = " , b*sin(spacing));
    
    for(i = [0:90:270]){
        rotate([0,0,45+i])translate([spacing+10,0,0])profile(l);
    }
}

// 20x20mm Aluminium extrusion generator
module profile(l=10){
    difference(){
        union(){
            translate([0,0,l/2-0.001/2])
            minkowski(){
                cube([20-2,20-2,l-0.001], center=true);
                cylinder(d=2,h=0.001);
            }
        }union(){
            for(i = [0:90:270]){
                rotate([0,0,i])
                hull(){
                    translate([0,9,l/2-0.1])cube([6,2,l+0.3],center=true);
                    translate([0,11,l/2-0.1])cube([9,2,l+0.3],center=true);
                }
            }
            translate([0,0,-0.1])cylinder(d=4.2, h=l+0.3);
        }
    }
}

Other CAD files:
CAD/stls/ligra_lava_disk_arm_l.stl
CAD/stls/ligra_lava_disk_motorgear.stl
CAD/stls/ligra_tripod_tripod_plate.stl
CAD/stls/ligra_stage_stage_motor_rot_rotor.stl
CAD/ligra_lava_disk.scad
CAD/gears.scad
CAD/ligra_lens.scad
CAD/ligra_misc.scad
CAD/ligra_par_spot.scad
CAD/ligra_projectorlens.scad
CAD/ligra_stage.scad
CAD/ligra_tripod.scad
CAD/stls/fd_back_conn.stl
CAD/stls/fd_frontcage_28_80.stl
CAD/stls/fd_frontcage_70_210.stl
CAD/stls/ligra_lens_frontcage_fd_28_80.stl
CAD/stls/ligra_lens_frontcage_fd_70_210.stl
CAD/stls/ligra_misc_foot.stl
CAD/stls/ligra_par_spot_stencil_cage.stl
CAD/stls/ligra_stage_stencil_cage.stl
CAD/stls/ligra_stage_stencil_cage_counter.stl

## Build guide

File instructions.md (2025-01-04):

# Instructions

This document shall serve as a comprehenive assembly-manual. Feel free to diverge at any point to build the ligra you want.

## Table of Contents

* [Preface](#preface)
* [Planning](#planning)
* [BOM](#bom)
* [3D-Prints](#3d-prints)
* [Required Tools](#required-tools)
* [Detailed Instructions](#detailed-instructions)
  * [Lens](#lens)
  * [Stage](#Stage)
  * [Light-Source](#light-source)
    * [PAR-Spot](#par-spot)
    * [Flashlight](#flashlight)
  * [Tripod-Mount](#tripod-mount)
  * [Interlock](#tripod-mount)
  * [Frame](#frame)
* [Assembly](#assembly)

## Preface

This guide assumes that you are building the same ligra as I did, I will try to make it clear, when something is either optional or specific to my hardware/your hardware. All in all I want to show you, how you can design your own projector, Gobo, light-graffiti, art-, whatever-light-machine. I want to show you, how you can bring a lens, a light source and something image forming together to crate something that allows you to be creative.

Each ligra consists of various parts that all invidially fulfill a purpose, all working together to make ligra what it is. Each part can be individually modified, build to purpose or replaced. I tried to reflect this by showing how to build each part, but also how to assemble all of them into ligra. Feel free to replace or modify any part that you need to have changed. One ligra basically consists of the frame, the light source, the stage (a stencil in my case), a tripod mount and the lens. You can see each of these as an assembly to be changed internally or as a whole, however, they all fulfill a purpose and cannot simply be removed.

## Planning

Given that this is rather an instruction on how to design and build various projectors instead of a speicific one, you should think about which tools you have at your disposal, what your targeted usecase may be and what materials you have and can work with. Before starting, read all the instructions and plan your ligra accordingly.

<table>
  <tbody>
    <tr>
      <td>
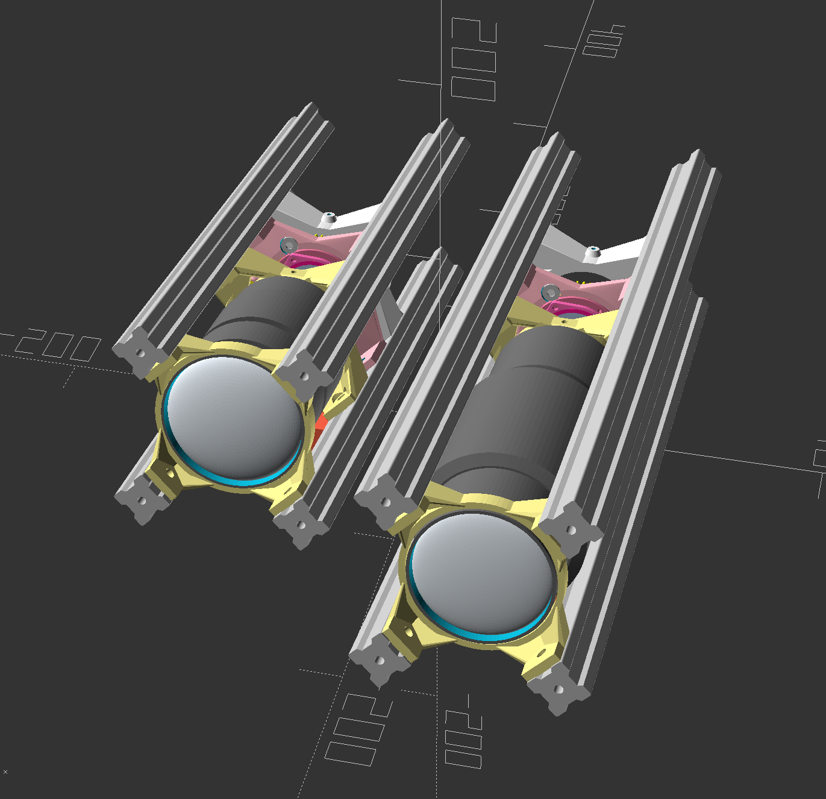
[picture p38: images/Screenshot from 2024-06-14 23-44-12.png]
        
      </td>
      <td>
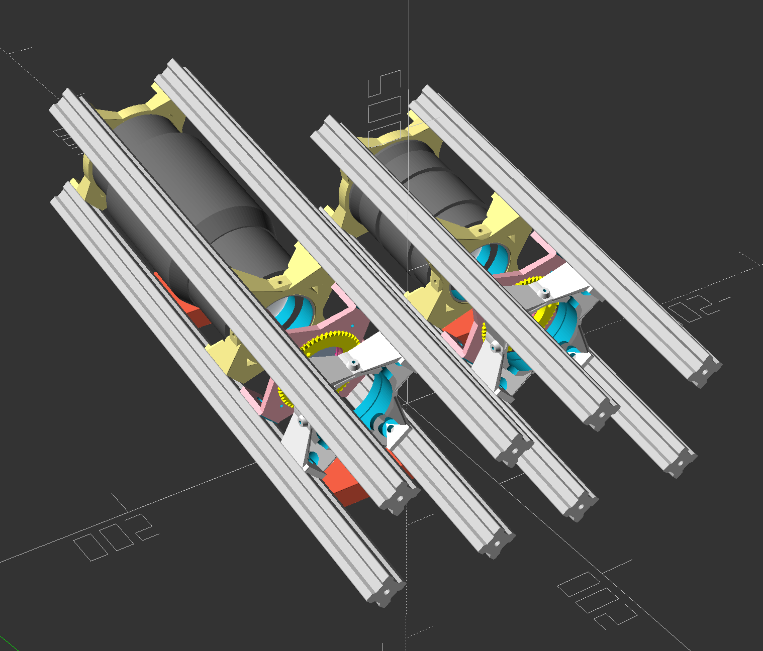
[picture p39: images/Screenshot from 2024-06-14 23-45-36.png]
        
      </td>
  </tr>
  <tr>
      <td colspan="2">
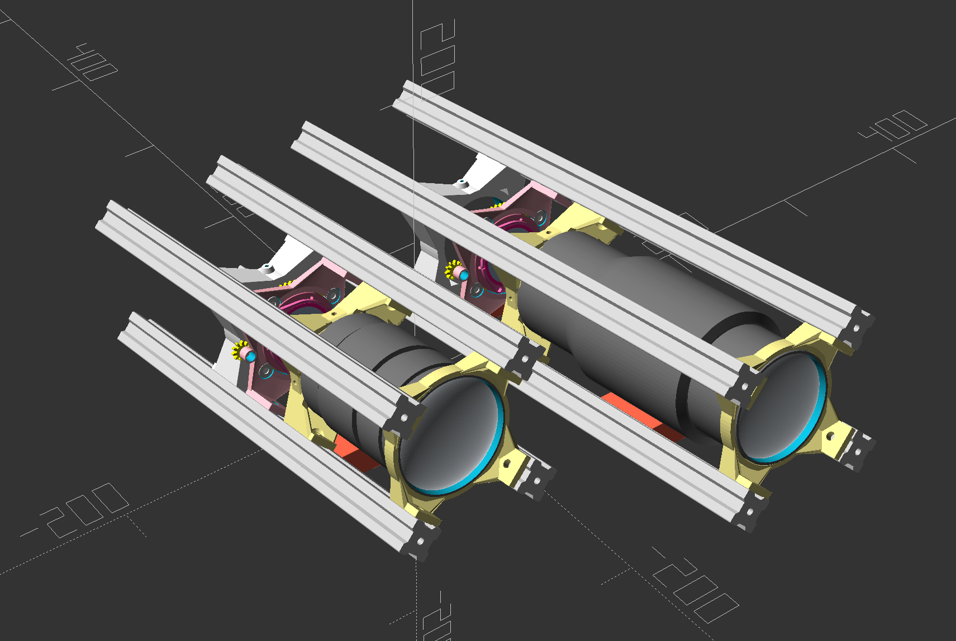
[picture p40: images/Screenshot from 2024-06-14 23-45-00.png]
        
      </td>
    </tr>
  </tbody>
</table>

Please consult the OpenSCAD script 'ligra.scad' for this phase aswell.

<table>
  <tbody>
    <tr>
      <td>
        
      </td>
    </tr>
  </tbody>
</table>

## BOM

For one ligra, you will need ruffly the following parts.
***
* 1 **Lens** (Canon FD works great here)
  * Low f-number is preferable (\<f4.0 ideally)
  * Variable focal legth preferred ([70-210mm](https://www.canonclassics.com/canon-nfd-70-210mm-f4/10-119/) works great for me, [28-85mm](https://volkergilbertphoto.com/canon-zoom-lens-fd-28-85-mm-f-4/) is nice for smaller rooms)
  * Full manual control is a must
  * Generally, the higher the focal legth, the farther away you can project something
* A matching (back-)lenscap
* A set of 3D prints to hold the lens in place ([see 3D prints](#3d-prints))
  * 1x [FD-cap to cage-mount](https://github.com/Jana-Marie/ligra/blob/main/CAD/stls/fd_back_conn.stl)
  * 1x Supporting FD-front-cage
    * [e.g. for 70-210mm](https://github.com/Jana-Marie/ligra/blob/main/CAD/stls/fd_frontcage_70_210.stl)
    * [e.g. for 28-85mm](https://github.com/Jana-Marie/ligra/blob/main/CAD/stls/fd_frontcage_28_80.stl)
***
* A **light source**
  * Can be a flashlight, a LED with a lens or anything that outputs a narrow and uniform (10-15°) beam of light
  * I use [a cheap 3W PAR spotlight](https://www.ebay.de/itm/314966001859) (yes it says 30W, but it consumes about 3W)
* 1x [3D printed Par spot holder](https://github.com/Jana-Marie/ligra/blob/main/CAD/stls/ligra_par_spot_stencil_cage.stl)
***
* 4x [20x20mm **aluminium extrusions**](https://www.motedis.com/en/Profile-20x20-B-type-slot-6)
  * 400mm length works great for most lenses
  * 300mm length works for 28-85mm lenses, but is a tight fit
* 16x nuts + bolts for said extrusions (likely M4 or M5)
***
* Optionally a set of 3D prints to hold the **stencil** in place ([see 3D prints](#3d-prints))
  * 1x [Stencil stage](https://github.com/Jana-Marie/ligra/blob/main/CAD/stls/ligra_stage_stage_motor_rot_base.stl)
  * 1x [Stencil rotor](https://github.com/Jana-Marie/ligra/blob/main/CAD/stls/ligra_stage_stage_motor_rot_rotor.stl)
  * 1x [Stencil gear](https://github.com/Jana-Marie/ligra/blob/main/CAD/stls/ligra_stage_stage_motor_rot_gear_l.stl)
  * A whole bunch of [Stencil-cages](https://github.com/Jana-Marie/ligra/blob/main/CAD/stls/ligra_stage_stencil_cage.stl) + [Cage-lids](https://github.com/Jana-Marie/ligra/blob/main/CAD/stls/ligra_stage_stencil_cage_counter.stl)
  * A whole bunch of 3mm diameter, 2mm height disc-magnets
  * 4x ballbearings with 4mm inner diameter, 9mm outer diameter and 3-4mm height
  * Some M3x16 screws
***
* Optionally [1 **front-PCB** as blind](https://github.com/Jana-Marie/ligra/tree/main/ligra_front)
  * 4x M5x16mm screws
  * 4x M5 washer
  * 4x [3D printed endcaps](https://github.com/Jana-Marie/ligra/blob/main/CAD/stls/ligra_misc_cap.stl)
***
* Optionally [1 **back-PCB** to drive the light source](https://github.com/Jana-Marie/ligra/tree/main/ligra_back)
  * 4x M5x16mm screws
  * 4x [3D printed endcaps](https://github.com/Jana-Marie/ligra/blob/main/CAD/stls/ligra_misc_cap.stl)
  * 4x [3D printed feet](https://github.com/Jana-Marie/ligra/blob/main/CAD/stls/ligra_misc_foot.stl)
***
* Optionally a [3D print](https://github.com/Jana-Marie/ligra/blob/main/CAD/stls/ligra_tripod_tripod_plate.stl) for a **tripod** to attach to
  * 4x sets of nuts + bolts for the extrusions
  * 1x [¼" thread insert](https://www.amazon.de/-/en/ruthex-Threaded-Insert-Bushings-Printing/dp/B09MTS6ZZQ/ref=sr_1_16)
* Optionally a tripod
***
* Optionally two [3D printed](https://github.com/Jana-Marie/ligra/blob/main/CAD/stls/ligra_interlock.stl) **interlocks** for stacking ligras
  * 4x sets of nuts + bolts for the extrusions
***

## 3D prints

[WIP]

Plesae print all 3D printed parts with the same technologie and materials to avoid missalingment due to material shrinkage.

## Required Tools

* Hex-drivers (or whichever screwhead you choose)
* M3, M5 tapping kit
* A set of drills
* 3D printer, FDM, SLA or SLS will do
* Exactor knife (for cleaning up 3D prints)
* Optionally a 2D printer for printing out stencils
  * See [Projection-Media](https://github.com/Jana-Marie/ligra/blob/main/projection-media.md)

## Detailed Instructions

With ligra, the aluminium extrusion will make up the whole frame, holding everything in place. However, all four extrusions are not connected to each other, except through all parts that they are supposed to hold. This means that we don't need extra parts that will make up the frame, but it also means that all parts within the frame, will become part of its structure. It is important, especially for the lens- and lamp-mount to be sturdy. In terms of assembly, this means that we need to prepare a few parts first, before putting them together in one go.

### Lens

**3D Print**

* 1x Supporting FD-front-cage
    * [e.g. for 70-210mm](https://github.com/Jana-Marie/ligra/blob/main/CAD/stls/fd_frontcage_70_210.stl)
    * [e.g. for 28-85mm](https://github.com/Jana-Marie/ligra/blob/main/CAD/stls/fd_frontcage_28_80.stl)
* 1x [FD-cap to cage-mount](https://github.com/Jana-Marie/ligra/blob/main/CAD/stls/fd_back_conn.stl)

**Parts**
signal-2025-01-04-134830_004.jpeg
* 1x FD-Lens
* 1x FD-Lenscap

While the lens can be seen as the heart of ligra, it actually is one of the simplest parts/steps here. Mostly because it already is a finished part that we don't really need to modify. We will just need to build a mount to fix it to the frame. Not only do we need a mount, this mount will be inegral to ligras structure and sturdyness, so let's keep it thicc and easy. To affic the lens to the mount you will need to drill out the back of the back-cap. It can then be affixed to the lens-mount and the lens can be screwed in.

<table>
  <tbody>
    <tr>
      <td>
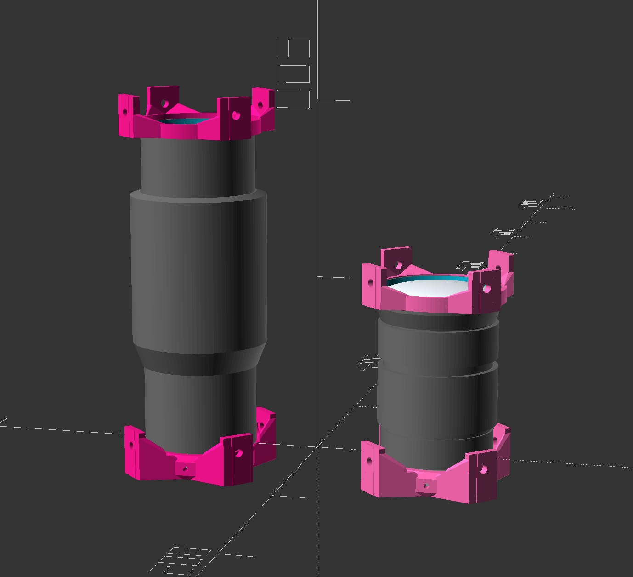
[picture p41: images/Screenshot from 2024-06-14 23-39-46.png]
        
      </td>
      <td>
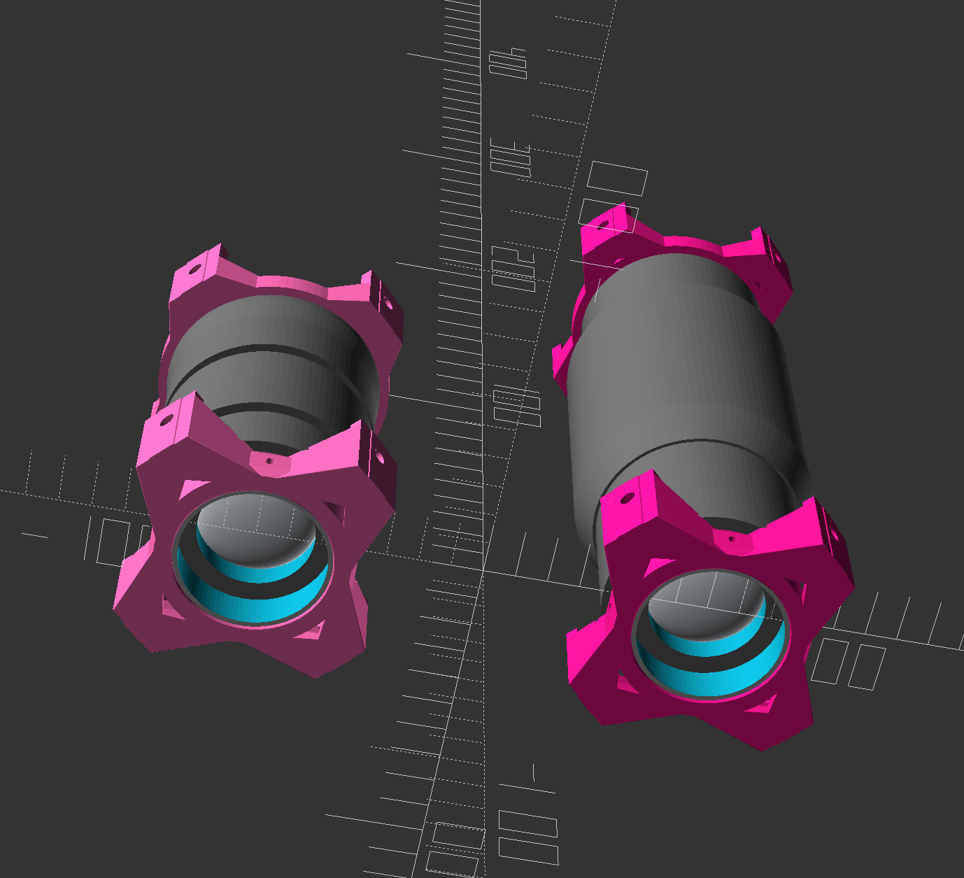
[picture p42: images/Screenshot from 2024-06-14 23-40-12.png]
        
      </td>
    </tr>
    <tr>
      <td>
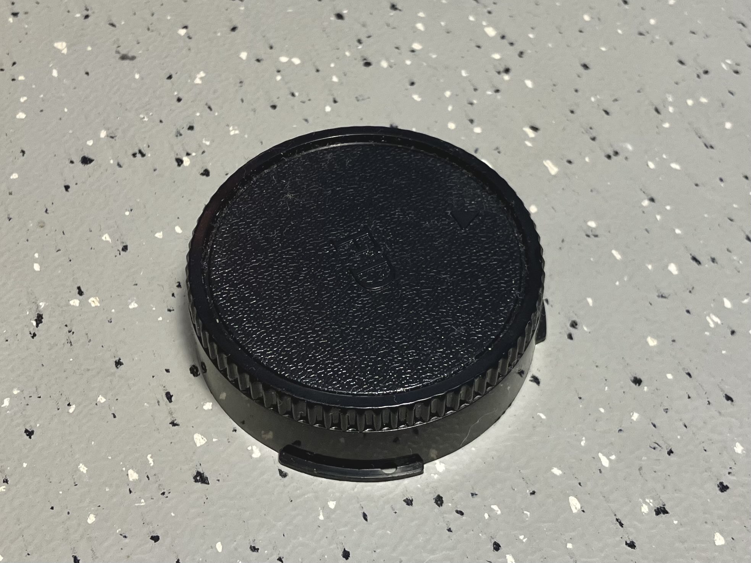
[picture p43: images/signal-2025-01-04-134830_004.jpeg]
        
      </td>
      <td>
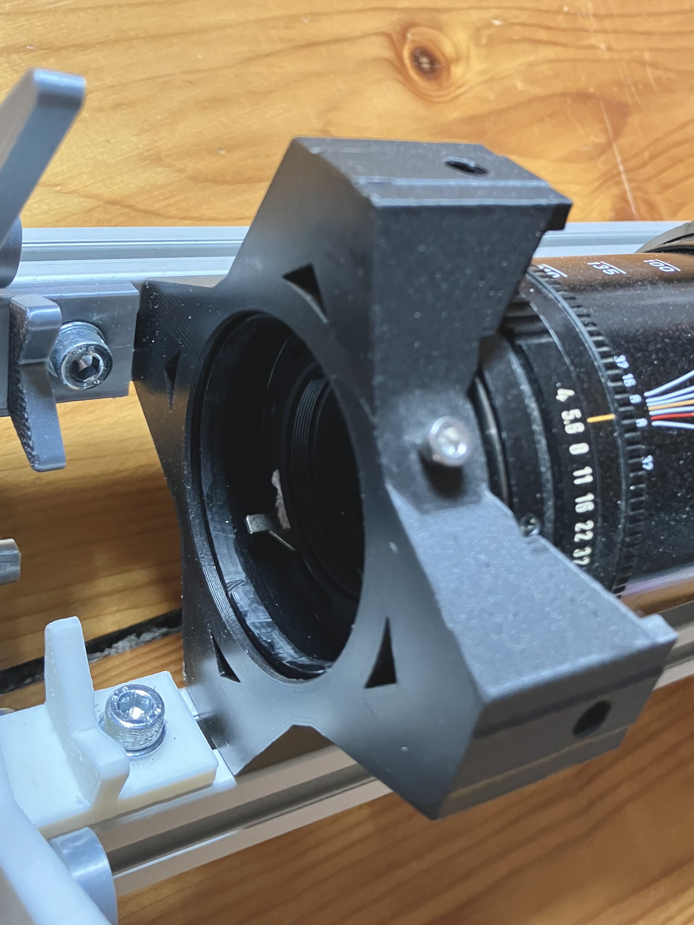
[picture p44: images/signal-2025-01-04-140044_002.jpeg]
        
      </td>
    </tr>
  </tbody>
</table>

Our lensmount will actually be made out of two 3D printed and one pre-fabricated part. The latter is a lenscap that we need to buy, pretty much any lenscap should do, I got mine from amazon. One of the 3D printed parts will be joined with the lenscap, firmly attaching lens and frame to each other. The second 3D printed part will be a more loose support of the lenses front opening, we don't want the full levering force of the lens being exorted into the rear mount. This mount however, cannot be fully fixed to the lens as it moves and turns during focus and focal-length change.

### Stage

**3D Print**

* 1x [Stencil stage](https://github.com/Jana-Marie/ligra/blob/main/CAD/stls/ligra_stage_stage_motor_rot_base.stl)
* 1x [Stencil rotor](https://github.com/Jana-Marie/ligra/blob/main/CAD/stls/ligra_stage_stage_motor_rot_rotor.stl)
* 1x [Stencil gear](https://github.com/Jana-Marie/ligra/blob/main/CAD/stls/ligra_stage_stage_motor_rot_gear_l.stl)
* A whole bunch of [Stencil-cages](https://github.com/Jana-Marie/ligra/blob/main/CAD/stls/ligra_stage_stencil_cage.stl) + [Cage-lids](https://github.com/Jana-Marie/ligra/blob/main/CAD/stls/ligra_stage_stencil_cage_counter.stl)

The stage ist probably the part where you can be the most creative, as already teased there are just so many ways of intercepting and transforming your light source. For more ideas, check out the [Projection-Media](https://github.com/Jana-Marie/ligra/blob/main/projection-media.md) page.

We will focus here on a, optionally motorized rotating stage, that hosts 2D laser-printed stencils. With stencil I mean foil that has been printed on. Initially I worked on 3-point rotary stage, which would allow for trapez correction. That idea got pushed to the back, to make room for a simpler stage, that is easier to iterate on. Eventually I will return to developing more stages. Check out the [Staging-Stages](https://github.com/Jana-Marie/ligra/blob/main/staging-stages.md) page.

<table>
  <tbody>
    <tr>
      <td>
        
      </td>
      <td>
        
      </td>
    </tr>
  </tbody>
</table>

The design I came up with is illustrated above. It is for the most part 3D printed, making production quite accessible to me. The light pink, big outer part will be screwed to the frame.

<table>
  <tbody>
    <tr>
      <td>
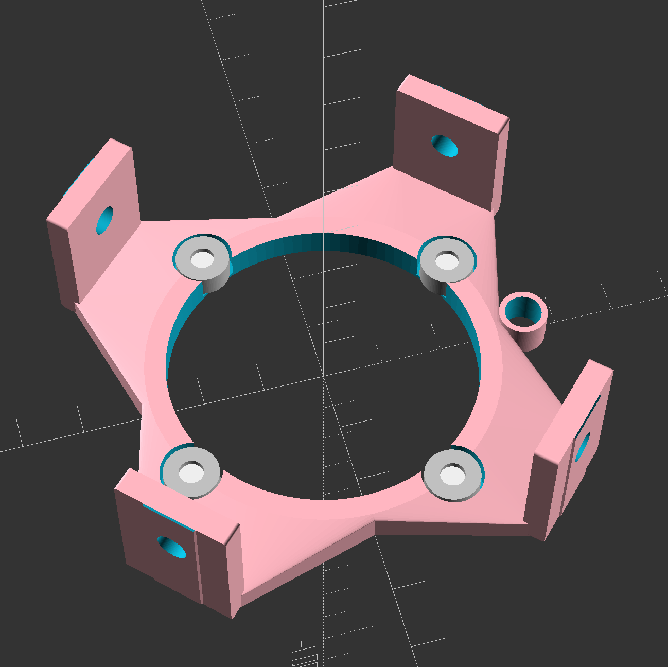
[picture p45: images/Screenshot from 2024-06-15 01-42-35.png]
        
      </td>
      <td>
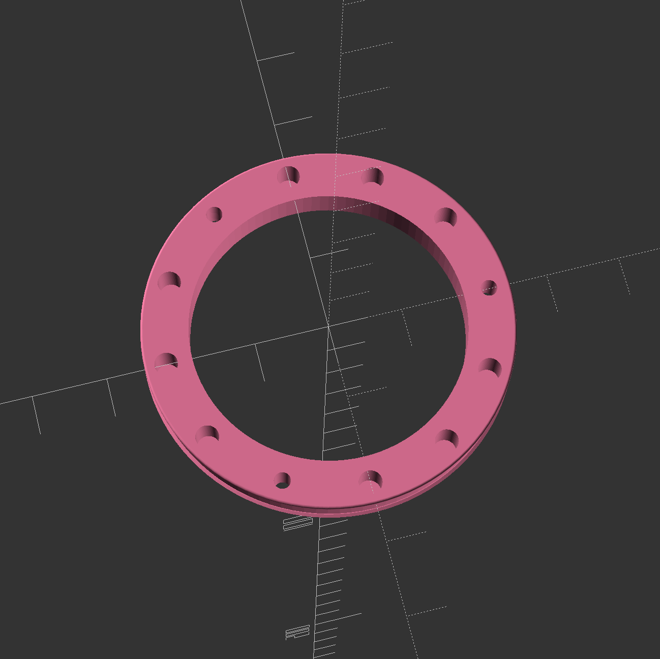
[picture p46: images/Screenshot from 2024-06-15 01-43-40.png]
        
      </td>
      <td>
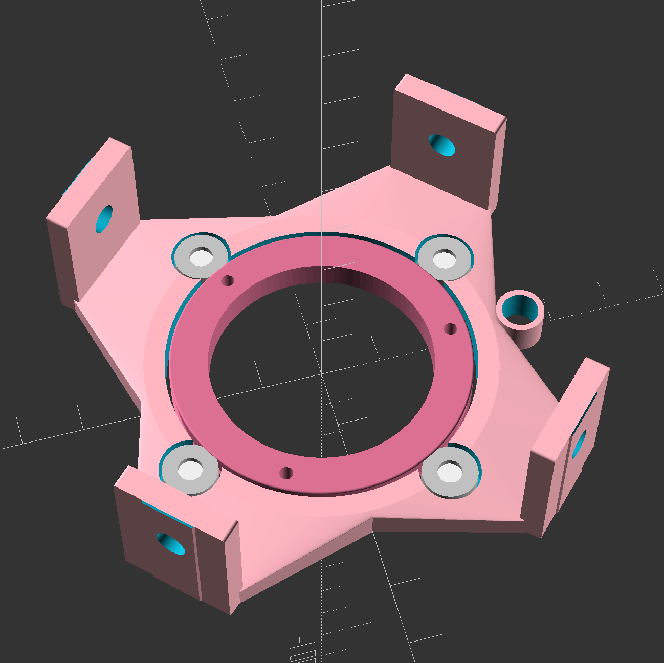
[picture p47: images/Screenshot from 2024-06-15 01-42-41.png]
        
      </td>
      <td>
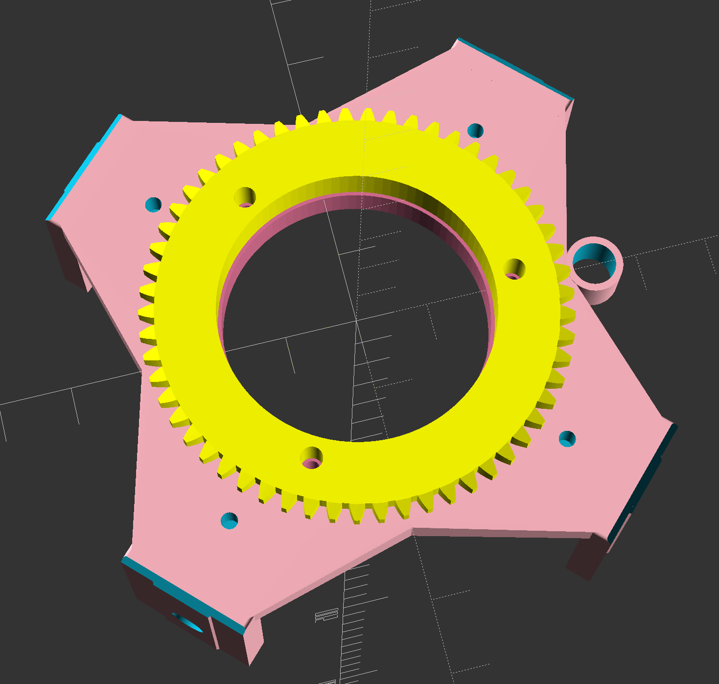
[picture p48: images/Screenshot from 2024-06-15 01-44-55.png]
        
      </td>
      <td>
        
      </td>
    </tr>
  </tbody>
</table>

It hosts 4 ball-bearings with an inner diameter of 4mm, an outer diameter of 9mm and a height of ~4mm. They will be pushed into place altogether with dark-pink ring into their respective slots. Before you do that, you should put 9 magnets with a size of 3mm diameter and 2mm height into the 9 larger slots of the inner ring. It's important that all magnets face the same direction! Since it is a tight fit, they all should stay in place, you can of course fill all slots up with some UV-cure resin or glue. Now you can gently push the ring and all four ball-bearings into place. Afterwards, turn over the assembly and screw the big yellow gear into the ring. You can ignore the small gear for now, it can be mounted to a motor and used to automatically turn the stencil this stage will host. If you don't need this, skip it, the big gear will still be handy for aligning the stencil manually

<table>
  <tbody>
    <tr>
      <td>
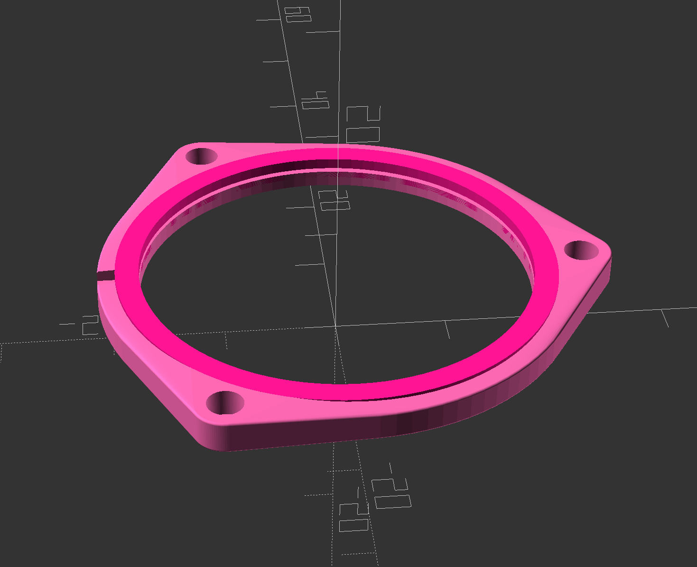
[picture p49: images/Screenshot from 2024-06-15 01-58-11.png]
        
      </td>
      <td>
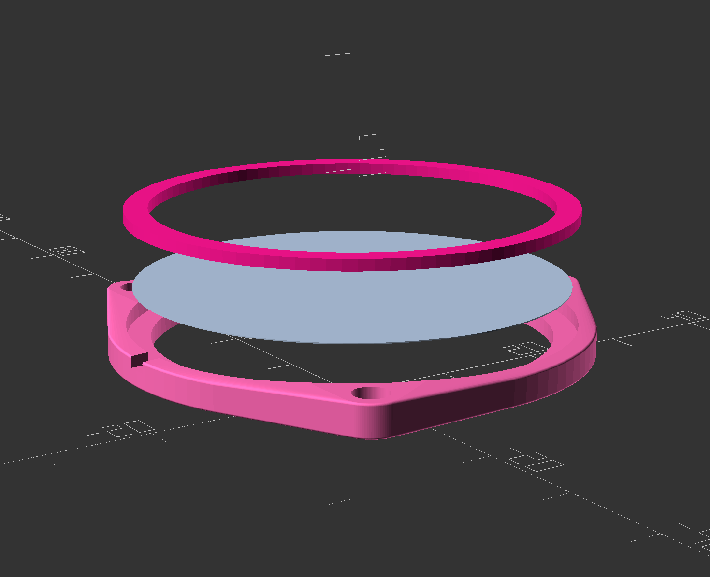
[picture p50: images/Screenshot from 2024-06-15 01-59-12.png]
        
      </td>
      <td>
        
      </td>
    </tr>
  </tbody>
</table>

Next up, you can print a whole bunch of these stencil frames. Each will clamp and hold one stencil, each will also host 3 magnets that allow the holder to snap to the stage. This allows for easy stencil preparation and exchange, just remove the old frame from the stage by hand, it will come right off and put a new one in place, it will gently snap to it. You can now go ahead and print stencils on foil, cut them and puit each into its own holder. Add the magnets in a similar fashion to what you did before, make sure that they all are aligned with your stage.

Your finished stage should look similiar to this. (Please ignore the frame in the last two images for now)

<table>
  <tbody>
    <tr>
      <td>
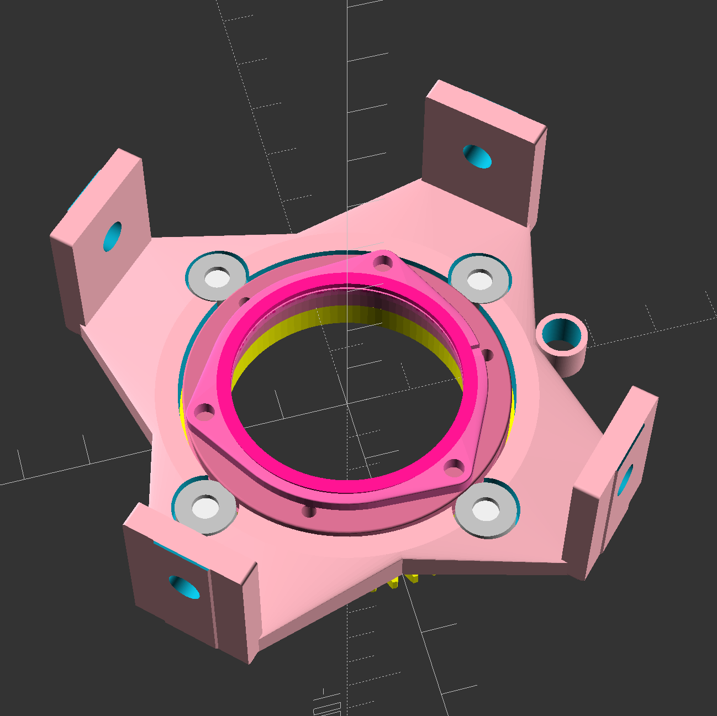
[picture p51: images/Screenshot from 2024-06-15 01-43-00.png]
        
      </td>
      <td>
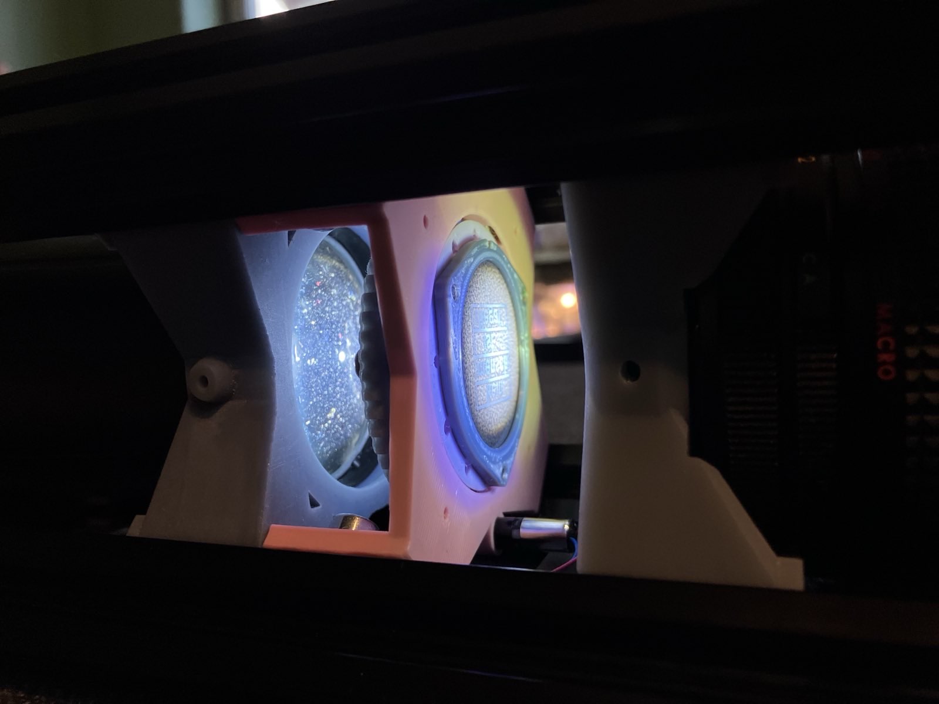
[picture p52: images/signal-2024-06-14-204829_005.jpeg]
        
      </td>
      <td>
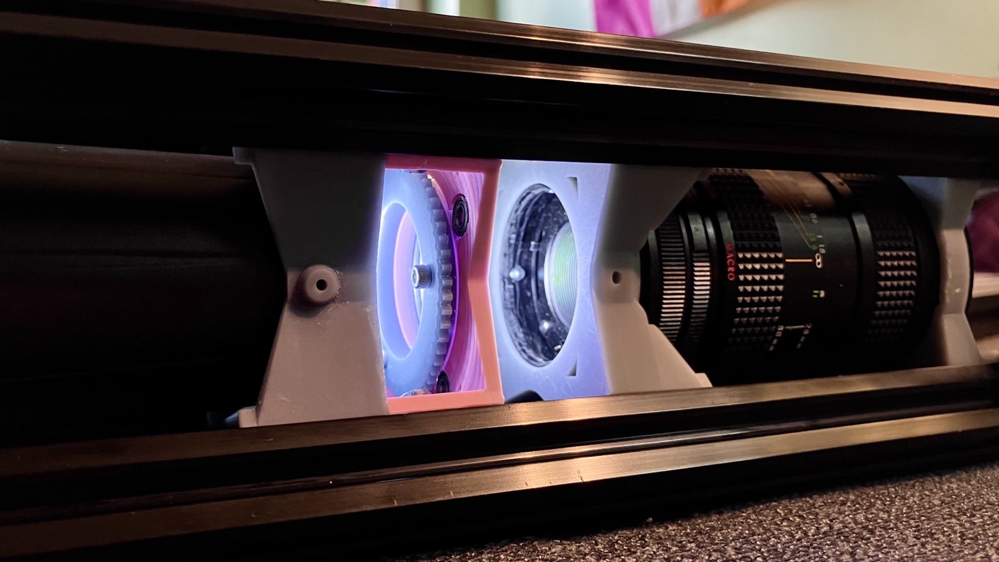
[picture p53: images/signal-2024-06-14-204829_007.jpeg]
        
      </td>
    </tr>
  </tbody>
</table>

### Light-Source

Depending on your light-source you will need a way of driving it. As I've choosen a 10W LED, I designed a board that can drive it from a USB power source, it is called the back-board and fully optional. [Back-Board](https://github.com/Jana-Marie/ligra/tree/main/ligra_back)

#### PAR-Spot

**3D Print**

1x [Par spot holder](https://github.com/Jana-Marie/ligra/blob/main/CAD/stls/ligra_par_spot_stencil_cage.stl)

**Parts**

1x [Par spot](https://www.ebay.de/itm/314966001859)
* 4x sets of nuts + bolts for the extrusions

<table>
  <tbody>
    <tr>
      <td>
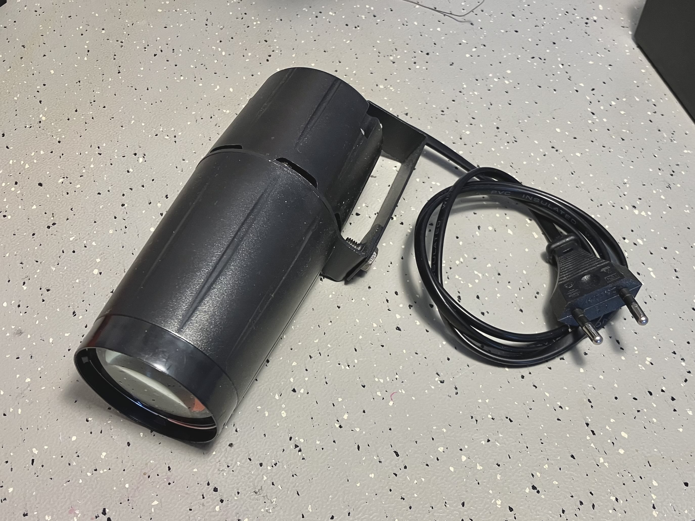
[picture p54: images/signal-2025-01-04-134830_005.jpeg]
        
      </td>
    </tr>
  </tbody>
</table>

#### Flashlight

In my earlier tests I used a flashlight as light-source and honestly I cannot recommend that enough if you are planning on testing the optical path. It's much easier to handle, easier to adapt and can freely held by hand at first. It helped me in establishing this project. I don't use it anymore, I've gotten myself a better light-source, still, I would like to quickly illuminate (heh!) its assembly.

<table>
  <tbody>
    <tr>
      <td>
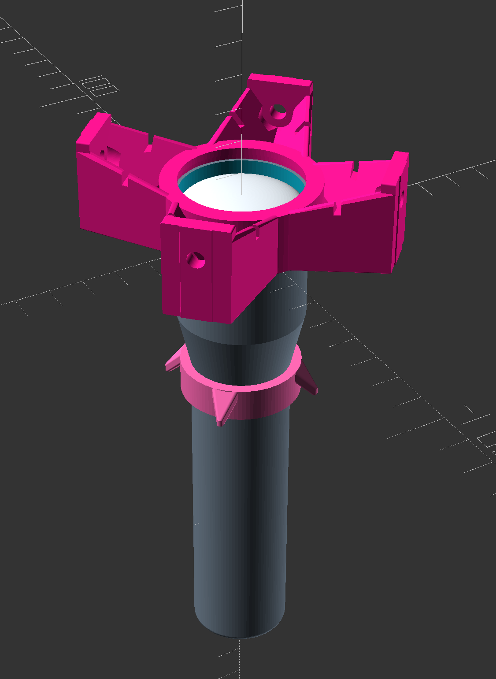
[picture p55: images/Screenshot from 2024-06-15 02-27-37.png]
        
      </td>
      <td>
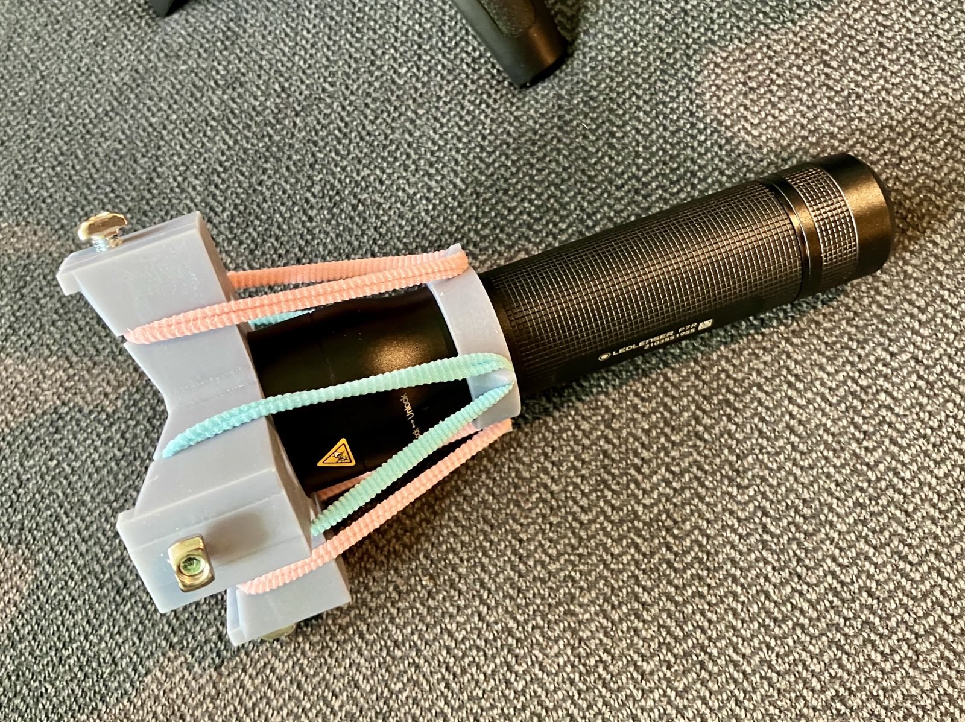
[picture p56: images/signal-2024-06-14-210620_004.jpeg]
        
      </td>
      <td>
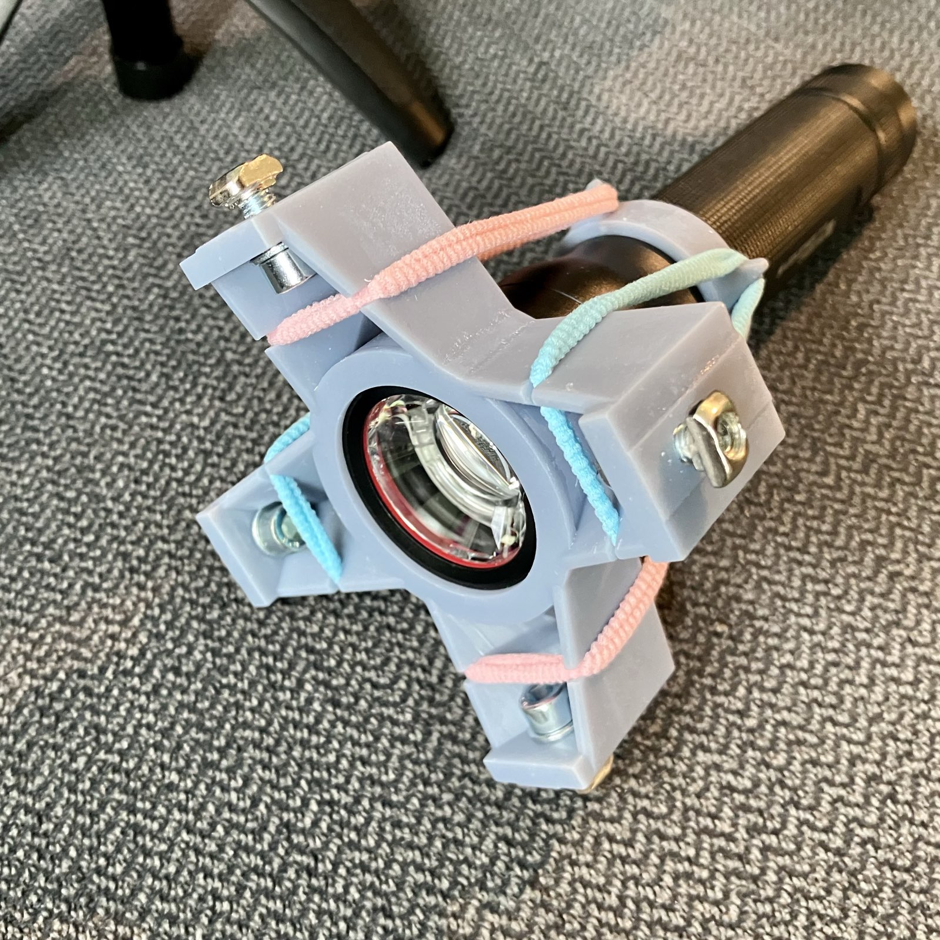
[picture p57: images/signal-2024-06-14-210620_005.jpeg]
        
      </td>
      <td>
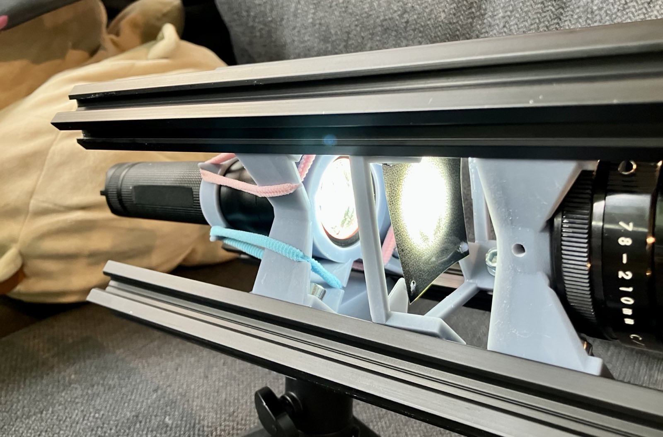
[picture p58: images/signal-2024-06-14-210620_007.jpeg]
        
      </td>
    </tr>
  </tbody>
</table>

It's quite simple and I don't think I need to explain a lot here, this LEDLenser flashlight is pressed into this simple block with four hair-ties and a counter-ring. This assembly is then asserted into ligra from the back. You can see on the last image, that this version is somewhat old already, based on the trivial, fixed stencil mount visible. 

### Tripod-Mount

**3D Print**

* 1x [Tripod-Plate](https://github.com/Jana-Marie/ligra/blob/main/CAD/stls/ligra_tripod_tripod_plate.stl)

**Parts**

* 1x [¼" thread insert](https://www.amazon.de/-/en/ruthex-Threaded-Insert-Bushings-Printing/dp/B09MTS6ZZQ/ref=sr_1_16
* 4x sets of nuts + bolts for the extrusions

<table>
  <tbody>
    <tr>
      <td>
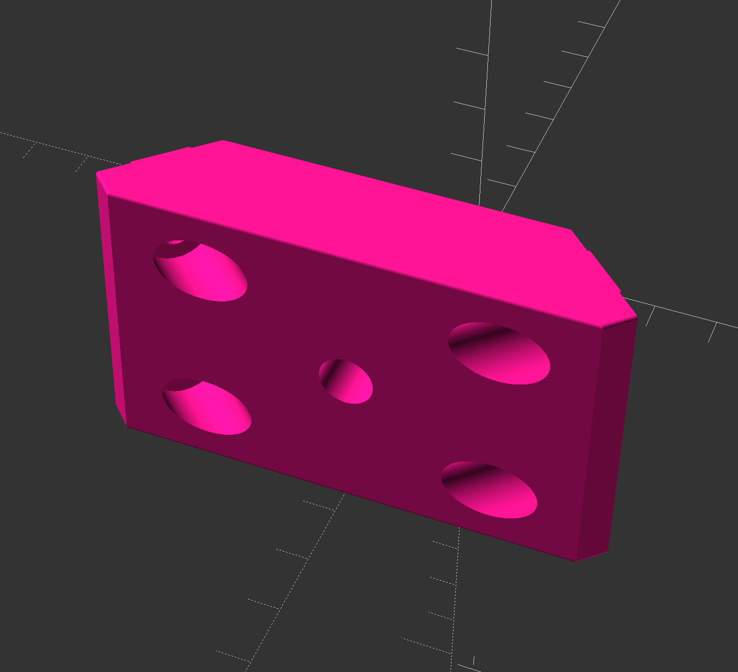
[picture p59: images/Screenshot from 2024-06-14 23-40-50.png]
        
      </td>
    </tr>
  </tbody>
</table>

A 3D printed plate that allows you to attach ligra to a typical tripod with a ¼" thread. The thread is a heat-insert, please make sure you sink it into the correct side of the 3D print. Also make sure the print is sturdy and the tripod is sufficient to support the weight. Screw the plate to the bottom of ligra, I usually like to start the whole build with this plate as it provides a solid base with two beams.

### Interlock

**3D Print**

* 2x [Interlock](https://github.com/Jana-Marie/ligra/blob/main/CAD/stls/ligra_interlock.stl)

**Parts**

* 4x sets of nuts + bolts for the extrusions

<table>
  <tbody>
    <tr>
      <td>
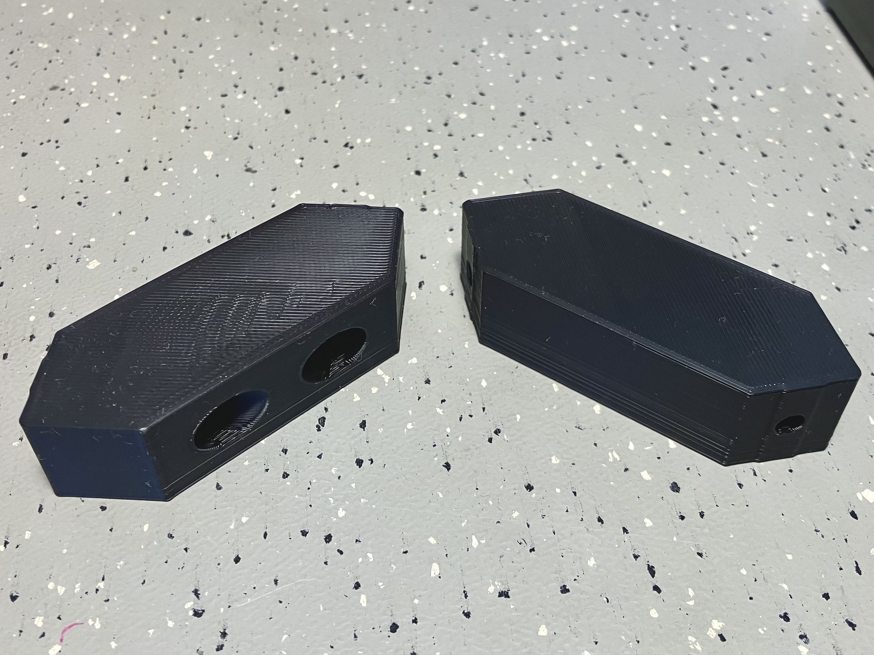
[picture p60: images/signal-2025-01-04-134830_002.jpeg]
        
      </td>
    </tr>
  </tbody>
</table>

A screw-in block that allows for easier stacking of ligras. There is not a whole lot behind it, besides alignemnt, please use tension straps to affix ligras together.

### Frame

After choosing the four alluminium extrusions you want to use, I recommend 20x20mm stock with a length of 400mm (for 70-210mm lenses) or 300mm (for 24-105mm lenses), you will need to tap both ends of each bar with a M5 tap. If you want to save on parts, you can reduce the build to just use the bottom extrusions.

<table>
  <tbody>
    <tr>
      <td>
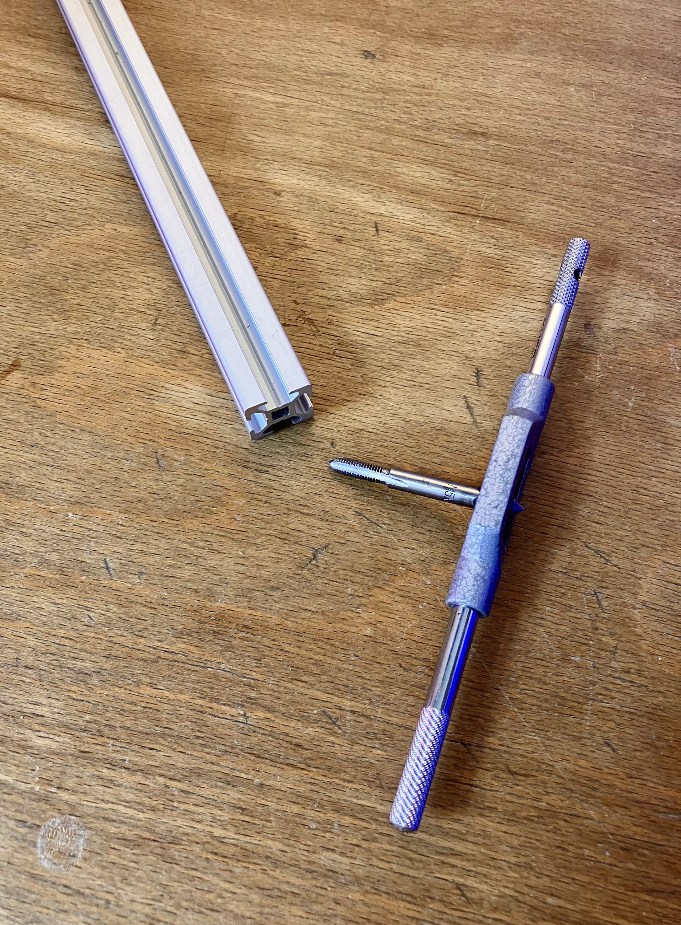
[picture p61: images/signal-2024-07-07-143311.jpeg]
        
      </td>
    </tr>
  </tbody>
</table>

## Assembly

**3D Print**

* 8x [3D printed endcaps](https://github.com/Jana-Marie/ligra/blob/main/CAD/stls/ligra_misc_cap.stl)
* 4x [3D printed feet](https://github.com/Jana-Marie/ligra/blob/main/CAD/stls/ligra_misc_foot.stl)

**Parts**

* 8x Bolts

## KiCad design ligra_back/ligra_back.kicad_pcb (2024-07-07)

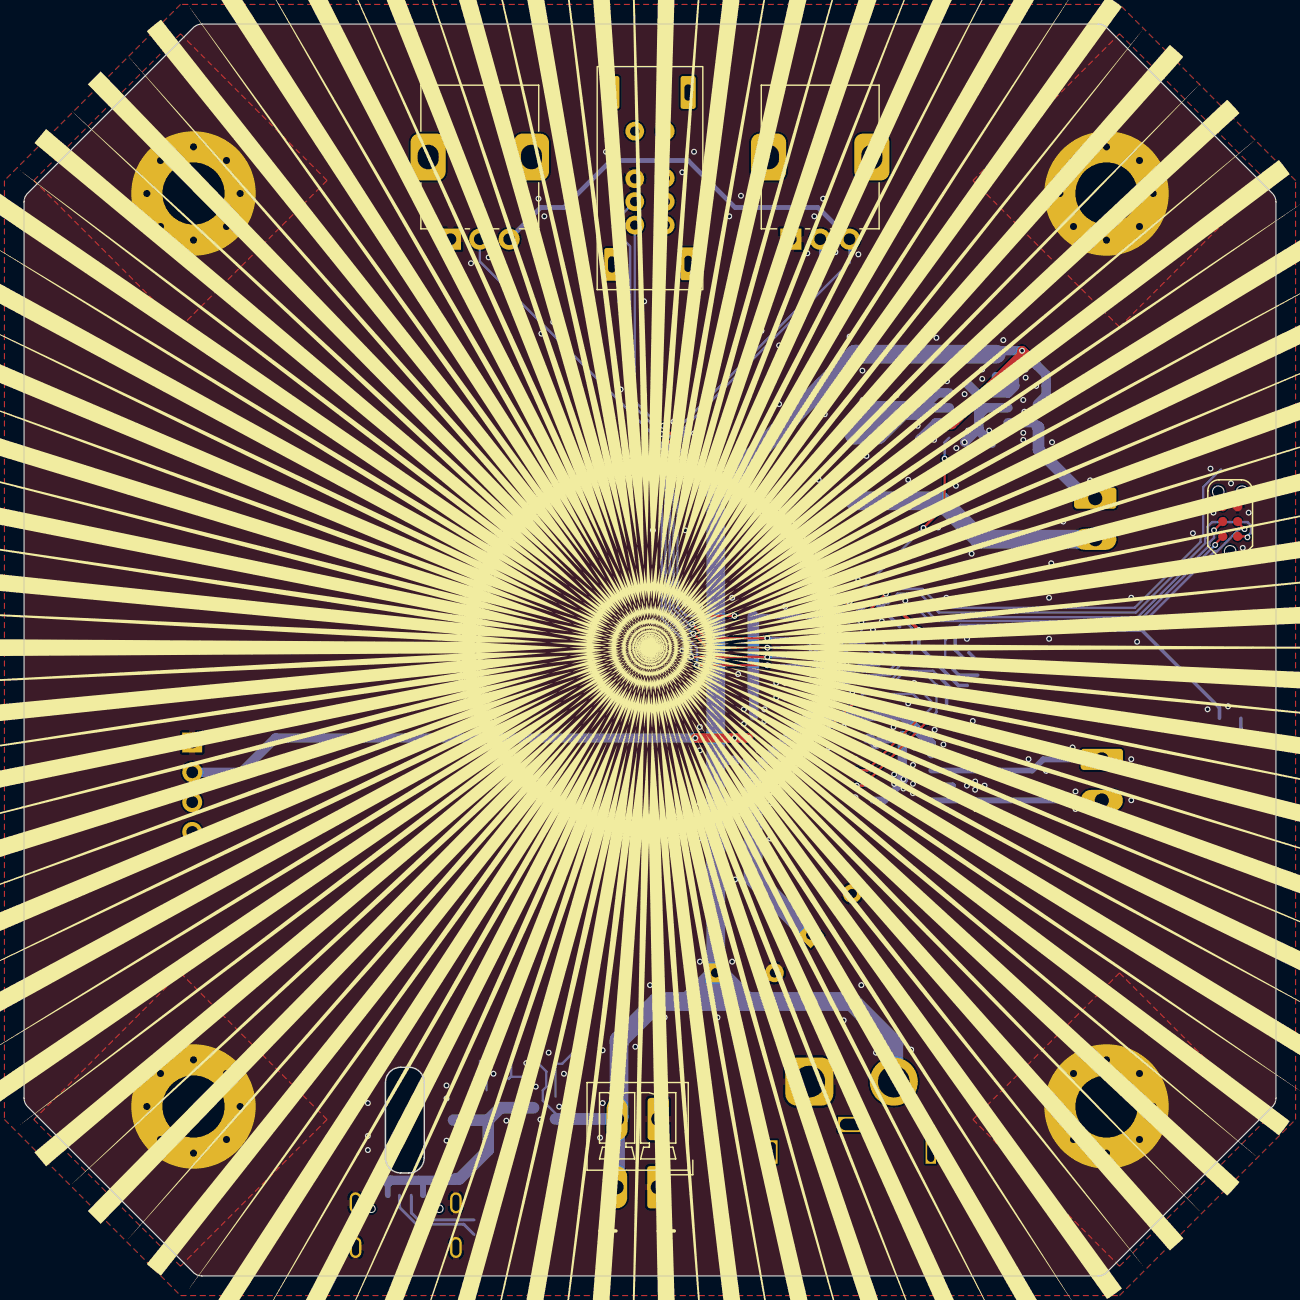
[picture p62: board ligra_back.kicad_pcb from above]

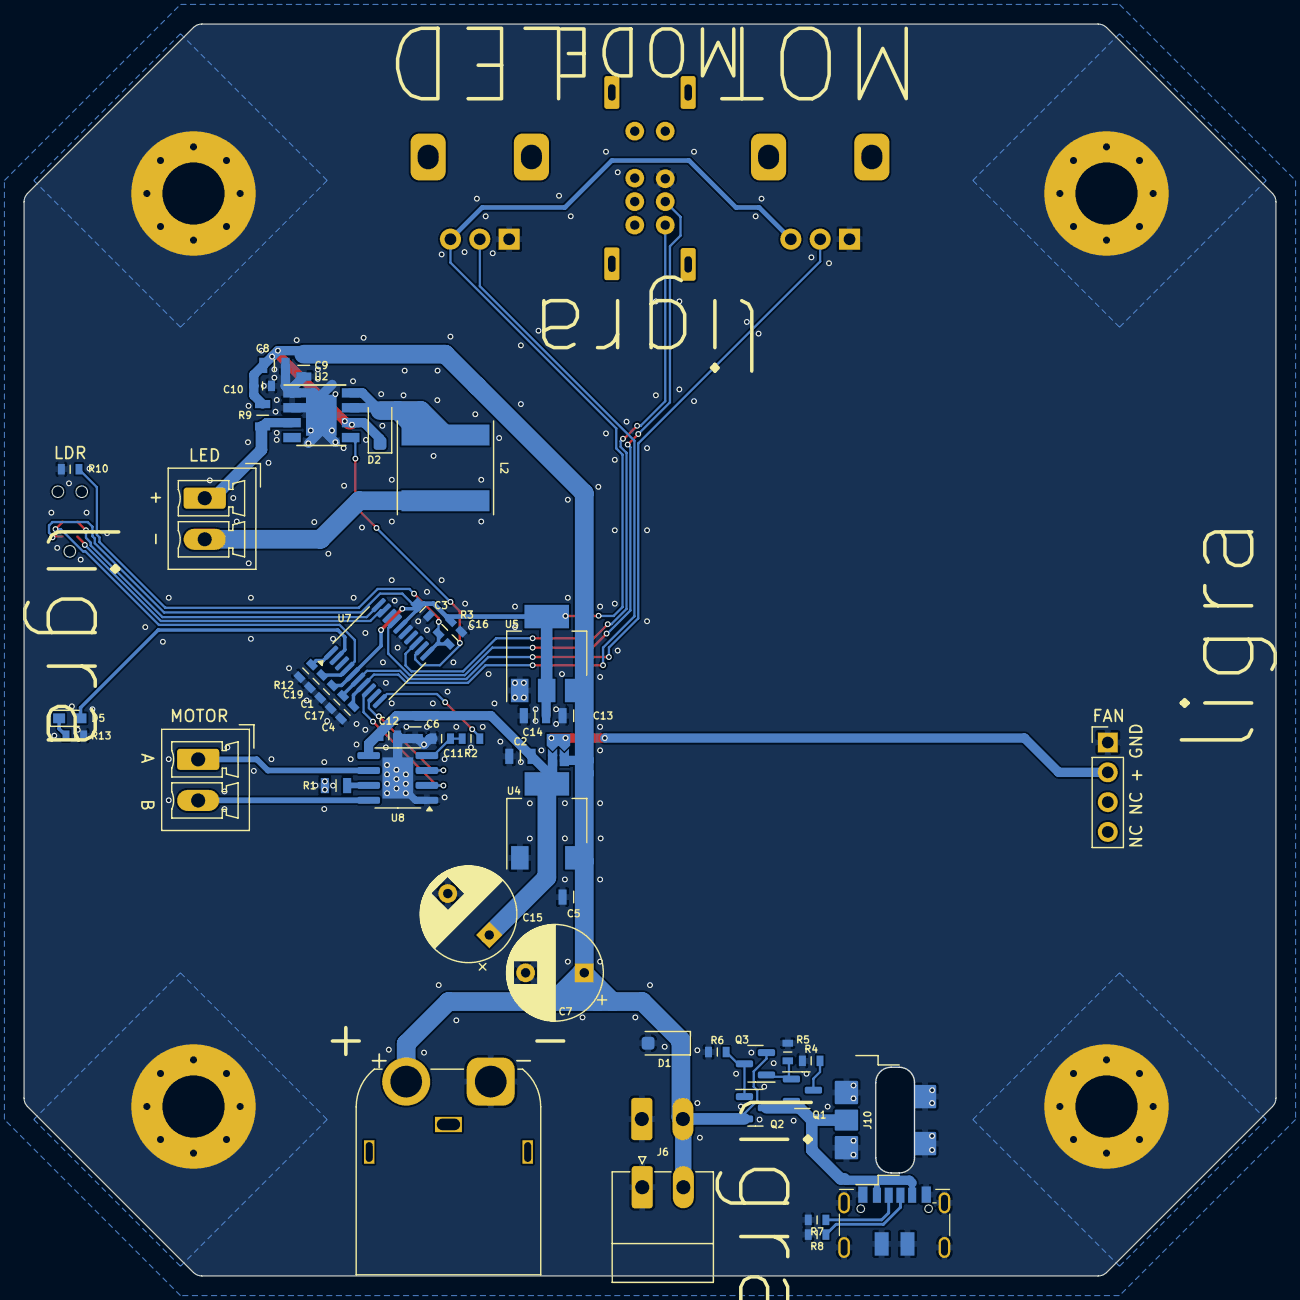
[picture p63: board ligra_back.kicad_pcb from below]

Board: 2 copper layers, 106.7 x 106.7 mm, 59 parts (50 on the bottom side), 33 nets.

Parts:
C1, C3, C4, C10, C11, C12, C16, C17, C19: 100n; C_0603
C2, C5, C6, C8, C9, C13, C14: 4u7; C_0805
C7, C15: 100u; CP_Radial_D8.0mm_P5.00mm
D1, D2: D210; D_SOD-123F
D5: LED; LED_0603_1608Metric
J1, J2, J3, J4: Mount; MountingHole_5.3mm_M5_Pad_Via
J5: POWER; PhoenixContact_MCV_1,5_2-G-3.5_1x02_P3.50mm_Vertical
J6: POWER; PhoenixContact_MC_1,5_2-G-3.5_1x02_P3.50mm_Horizontal
J7: LED; PhoenixContact_MCV_1,5_2-G-3.5_1x02_P3.50mm_Vertical
J8: FAN; PinHeader_1x04_P2.54mm_Vertical
J9: Motor; PhoenixContact_MCV_1,5_2-G-3.5_1x02_P3.50mm_Vertical
J10: USB-vertical_footprint; USB-C-vertical_footprint
J11: USB_C_Receptacle_PowerOnly_6P; USB-C_Power
J12: XT60; AMASS_XT60IPW-M_1x03_P7.20mm_Horizontal
JP1: jmp; JMP_2_1
L2: 47uF; L_Taiyo-Yuden_NR-80xx
P1: TC2030-CTX-Tag-Connect; TC2030
Q1, Q3: BC807; SOT-23
Q2: AO3401A; SOT-23
R1, R9: R33; R_0805
R2, R3, R4, R5, R6, R7, R8, R12, R13: 5k1; R_0603
R10: LDR; R_0603
RV1, RV2: 10k; Potentiometer_Alps_RK09K_Single_Vertical
SW2: SW_SP3T; SW_3S
U2: AL8843; Diodes_SO-8EP
U4: NCP1117-12_SOT223; SOT-223-3_TabPin2
U5: NCP1117-3.3_SOT223; SOT-223-3_TabPin2
U7: STM32F030F4Px; TSSOP-20_4.4x6.5mm_P0.65mm
U8: DRV8231; SOIC-8-1EP_3.9x4.9mm_P1.27mm_EP2.62x3.51mm

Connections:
+3V3: C1.2, C3.2, C14.2, P1.1 (VCC), R3.2, RV1.3, RV2.3, U5.2 (VO), U7.5 (VDDA), U7.16 (VDD)
+12V: C2.2, C6.2, C12.1, C15.1, JP1.1 (A), U4.2 (VO), U8.5 (VM)
GND: C1.1, C2.1, C3.1, C4.1, C5.1, C6.1, C7.2, C8.1, C9.1, C10.1, C11.1, C12.2, C13.2, C14.1, C15.2, C16.1, C17.1, C19.1, D1.2 (A), J1.1, J2.1, J3.1, J4.1, J5.1, J6.1, J8.1, J10.1 (GND), J10.S1 (GND), J11.A12 (GND), J11.B12 (GND), J11.S1 (SHIELD), J12.1, P1.5 (GND), R1.2, R4.1, R5.1, R6.1, R7.2, R8.2, R10.1, R12.1, R13.1, RV1.1, RV2.1, SW2.3, U2.1 (GND), U2.2 (GND), U2.9 (GND), U4.1 (GND), U5.1 (GND), U7.15 (VSS), U8.1 (GND), U8.9 (GND)
LED_CONTROL: U2.5 (CTRL), U7.12 (PA6)
NRST: C19.2, P1.3 (~RESET), U7.4 (NRST)
unnamed: D2.2 (A), L2.1, U2.7 (SW), U2.8 (SW)
unnamed: D5.2 (A), U7.2 (PF0)
unnamed: D5.1 (K), R13.2
unnamed: J7.1, R9.2, U2.3 (SET)
unnamed: J7.2, L2.2
unnamed: J8.2, JP1.2 (C)
unnamed: J9.1, U8.6 (OUT1)
unnamed: J9.2, U8.8 (OUT2)
unnamed: J10.2 (VBUS), J11.A9 (VBUS), J11.B9 (VBUS), Q1.2 (E), Q2.3 (D)
unnamed: J11.A5 (CC1), R7.1
unnamed: J11.B5 (CC2), R8.1
unnamed: Q1.1 (B), Q3.1 (B), R5.2
unnamed: Q1.3 (C), R4.2
unnamed: Q2.1 (G), Q3.3 (C), R6.2
unnamed: R12.2, U7.1 (BOOT0)
unnamed: C17.2, RV2.2, U7.6 (PA0)
unnamed: C4.2, RV1.2, U7.7 (PA1)
unnamed: U7.8 (PA2), U8.2 (IN2)
unnamed: U7.9 (PA3), U8.3 (IN1)
unnamed: R2.1, U7.10 (PA4)
unnamed: C16.2, R3.1, R10.2, U7.11 (PA5)
unnamed: SW2.1, U7.13 (PA7)
unnamed: SW2.2, U7.17 (PA9)
unnamed: R1.1, U8.7 (ISEN)
unnamed: C11.2, R2.2, U8.4 (VREF)
SWCLK: P1.4 (SWCLK/TCK), U7.20 (PA14)
SWDIO: P1.2 (SWDIO/TMS), U7.19 (PA13)
VBUS: C5.2, C7.1, C8.2, C9.2, C10.2, C13.1, D1.1 (K), D2.1 (K), J5.2, J6.2, J12.2, JP1.3 (B), Q2.2 (S), Q3.2 (E), R9.1, U2.6 (VIN), U4.3 (VI), U5.3 (VI)

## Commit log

2024-06-01 added ligra pcbs
    [ligra_back.kicad_pcb, ligra_back.kicad_sch, ligra_front.kicad_sch]
2024-06-01 added 3D files
    [cap.scad, end_cap.stl, foot.stl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]
2024-06-14 added PCB graphics
2024-06-14 added pcb readmes
2024-06-14 added more stls
    [fd_back_conn.stl, fd_frontcage_28_80.stl, fd_frontcage_70_210.stl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]
2024-06-14 big CAD refactor, CAD cleanup
    [ligra.scad, ligra_flashlight.scad, ligra_frame.scad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]
2024-06-14 removed old files
    [cap.scad]
2024-06-14 cleaned up stage
    [ligra.scad, ligra_stage.scad]
2024-06-15 added stage instructions
2024-06-15 updated stage
2024-06-15 worked on the lensmount
2024-06-15 added staging-stages
2024-06-15 worked on stages
2024-06-15 added pcb, improved view
    [ligra.scad, ligra_misc.scad]
2024-07-07 updated STLs, added new ones, removed old oneas
    [ligra_lens.scad, ligra_lens_frontcage_fd_28_80.stl, ligra_lens_frontcage_fd_70_210.stl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]
2024-07-07 updated back to v1.2.0
    [ligra_back.kicad_pcb, ligra_back.kicad_sch]
2025-01-04 added lava-disk
    [ligra_lava_disk.scad]
2025-01-04 updated files
    [ligra_flashlight.scad, ligra_lens.scad, ligra_par_spot.scad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]
2025-01-04 added more lens stls
    [ligra_lens_frontcap_35-105.stl, ligra_lens_frontcap_38-95.stl, ligra_lens_lenscagefd.stl]
2025-01-04 added interlock
    [ligra_interlock.stl]
